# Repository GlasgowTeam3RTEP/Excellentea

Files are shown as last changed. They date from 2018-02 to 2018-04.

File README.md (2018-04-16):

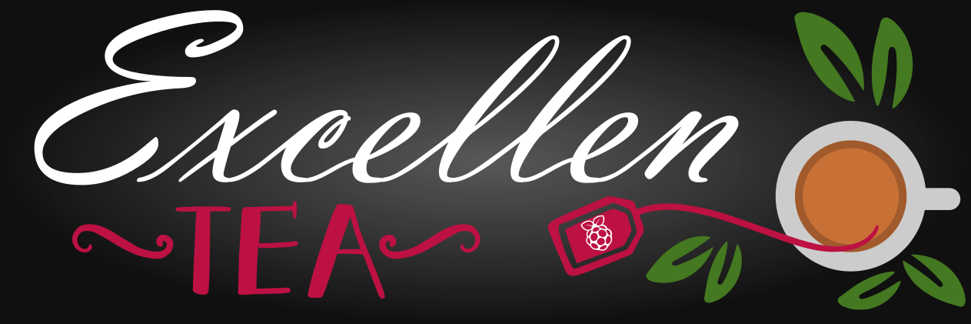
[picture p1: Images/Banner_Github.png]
Excellentea


# Description

Excellentea is an automatic tea maker. The user can operate the machine remotely through an online interface. 
In other words, you can order your tea, by chosing from several modes, as you leave work and find it ready when you get home. 
An LCD display provides feedback of the progress status. 

# Installation

## Prerequisites
The application requires the user to have Apache and php installed on their Raspberry Pi. Use your favourite package manager to install the packages _apache2_ and _php_ or, alternatively, open the terminal and use the commands below.
```
sudo apt-get update
sudo apt-get install apache2 php libapache2-mod-php -y
```
The One-wire and I2C protocols must be activated for the application to work. Run the following command:
```
sudo raspi-config
```
and navigate to _Interfacing options_ to enable _I2C_ and _1-Wire_.

## Installation procedure
Clone the repository to your Raspberry Pi and run the following commands:
```
./configure
make
make install
```
Initialise and start the apache web interface (change the default pi with your user name):
```
sudo chown -R pi /var/www/html/
rm /var/www/html/index.html
cp GUI/* /var/www/html/
sudo reboot
```
Find your local IP with:
```
hostname -I
```
The program can then be started by running the command
```
sudo excellentea
```
from the terminal, and the web interface will be available at the IP address found previously. The web interface can then be accessed by external hosts by enabling router port forwarding.

# Usage
[//]: # (instruct other people on how to use your project after they’ve installed it)

1. Load your cup with water

2. Load your tea infuser with the tea of your choice

3. Activate the tea maker from the online user interface

4. Choose the brewing mode of your tea

5. Wait...tea is ready:)

Watch Excellentea in action:
<p align="center">
<a href="http://www.youtube.com/watch?feature=player_embedded&v=Yk8ouI6cpxk
" target="_blank">Click to play</a>
</p>

# Configuration
An in-depth description of the project can be found on our [wiki](https://github.com/GlasgowTeam3RTEP/Excellentea/wiki). The following sections will briefly describe the main components and their implementation in the overall design. 

## Hardware

### Key components
- 1 Raspberry PI microcontroller board (tested on version 3 Model B)
- 1 Stepper motor (MIKROE-1530)
- 1 Digital temperature sensor (ds18b20)
- 12V DC power supply 
- 1 heating element (12V) (B004O8BGXE)
- 1 tea infuser 
- 1 reed float sensor (59630)
- 2 Darlington transistor array (ULN2803A)
- LCD
- 2 N-channel logic-level MOSFET (FQP30N06L)
- MOSFET heat sink (507222B00000G)

### Additional components
The project also requires standard passive components (e.g. resistors), prototyping tools (e.g. breadboard/pcb) and materials for the encasing. Check out our [wiki](https://github.com/GlasgowTeam3RTEP/Excellentea/wiki) for details. 

### Protocol
The digital temperature sensor DS18B20 communicates with the board through the one-wire protocol on pin 7 (BCM4). The reed float sensor only outputs two-states so a communication protocol is not required. 

## Software
The software was written to reflect the data flow depicted below. The float switch is used as a safety feature to ensure that the heating element cannot be switched on in the absence of water. Once the cup is full of water, the program will wait for a user interaction through the web interface. The main program will receive the signal to initiate the tea making procedure, using a temporary communication file, with two main parameters, the brewing temperature and the brewing time. The heating element is turned on and the temperature is monitored periodically via the sensor on the One-wire bus. Once the temperature reaches the desired value, the heating element is switched off and the preloaded tea infuser is lowered by the stepper motor. Once the desired brewing time has elapsed, the stepper motor rewinds the strainer and the tea is ready. Full software documentation can be found [here](https://glasgowteam3rtep.github.io/Excellentea/).

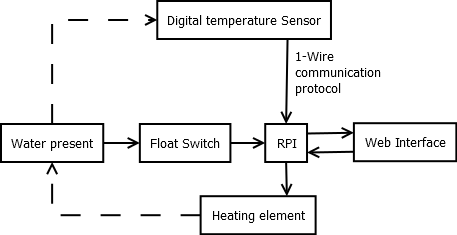
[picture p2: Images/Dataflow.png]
Data Flow Flow diagram of the tea maker


# Authors
* [**Andrea Spanou**](https://github.com/andreaspanou) - *Initial work* 
* [**Ciaran McGeady**](https://github.com/CiaranAnthony) - *Initial work*
* [**Simone Marcigaglia**](https://github.com/SimoneMarcigaglia) - *Initial work*

See also the list of [contributors](https://github.com/GlasgowTeam3RTEP/ExcellenTea/contributors) who participated in this project. Check out our [Twitter](https://twitter.com/Excellentea1) page to be up-to-date with the latest developments!

# Contributing

Please read [CONTRIBUTING.md](CONTRIBUTING.md) for details on our code of conduct, and the process for submitting pull requests to us.

# License

This project is licensed under the MIT License - see the [LICENSE](LICENSE) file for details.

# Acknowledgments

We would like to thank the weather in Glasgow for making us think about tea all the time.

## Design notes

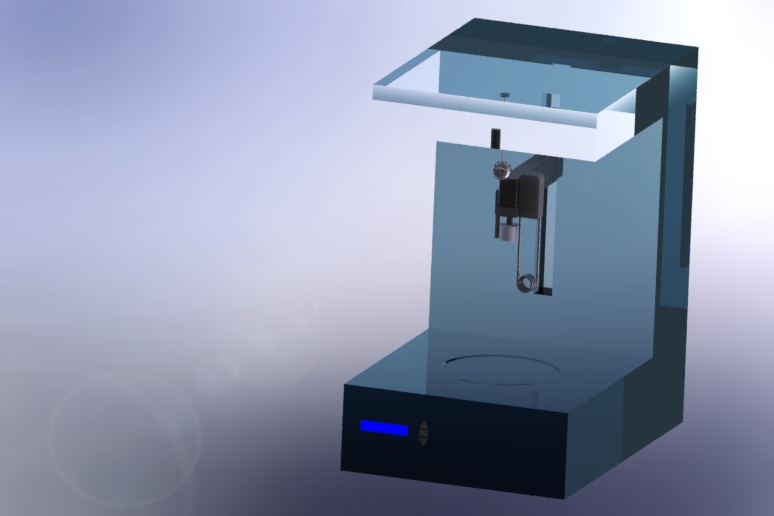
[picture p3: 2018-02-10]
Images/conceptual_design.JPG

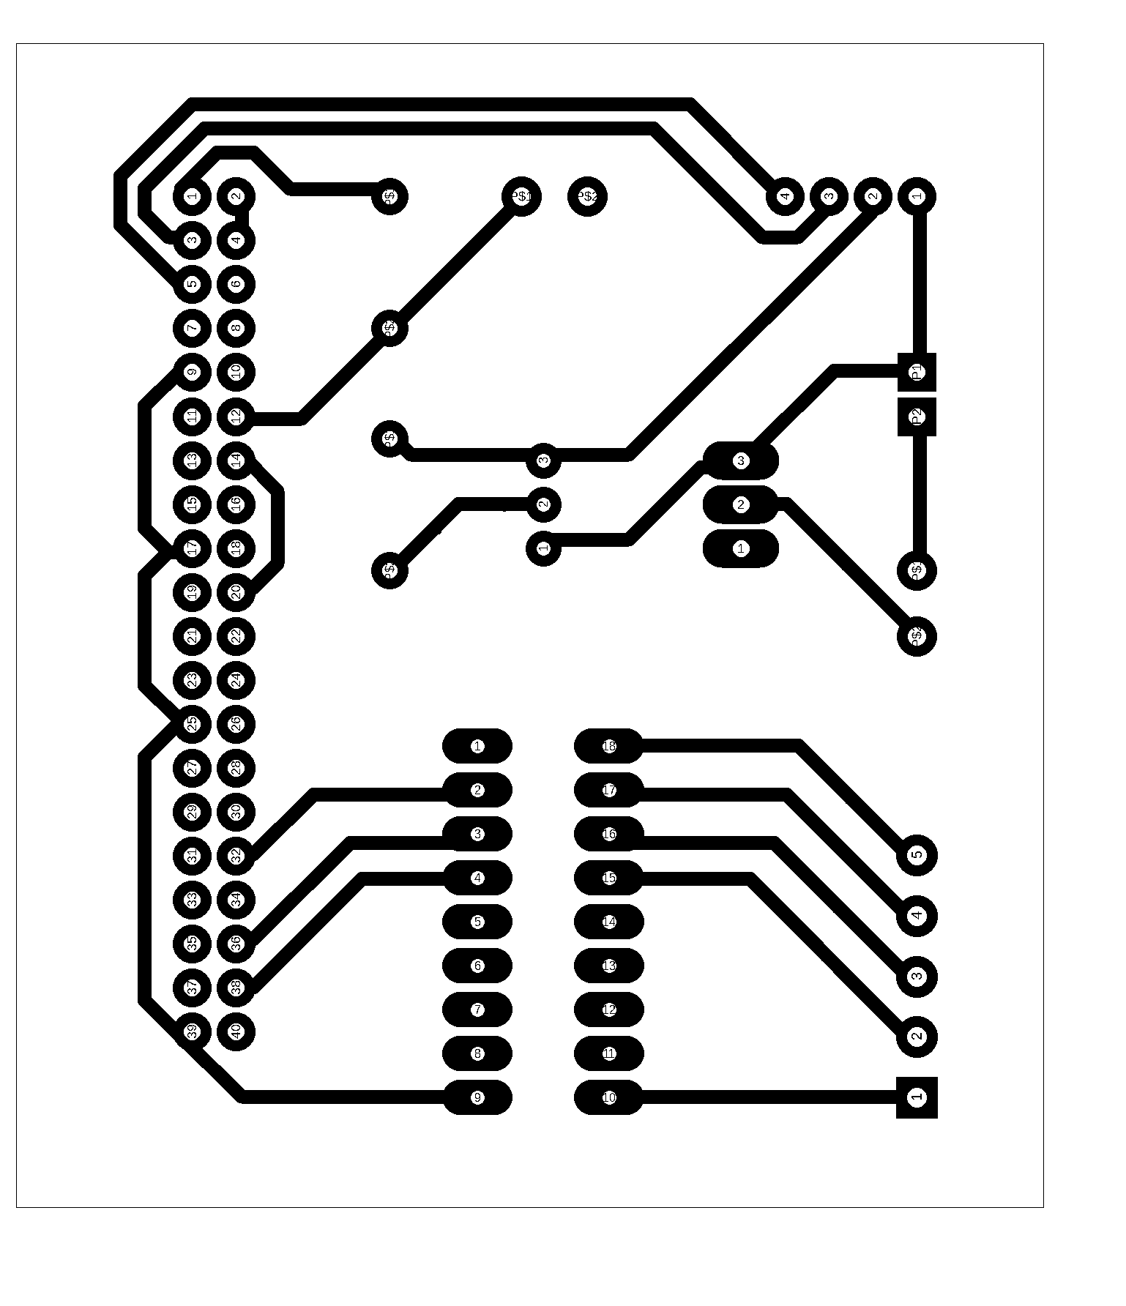
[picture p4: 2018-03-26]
Schematics/PCB_Top.png

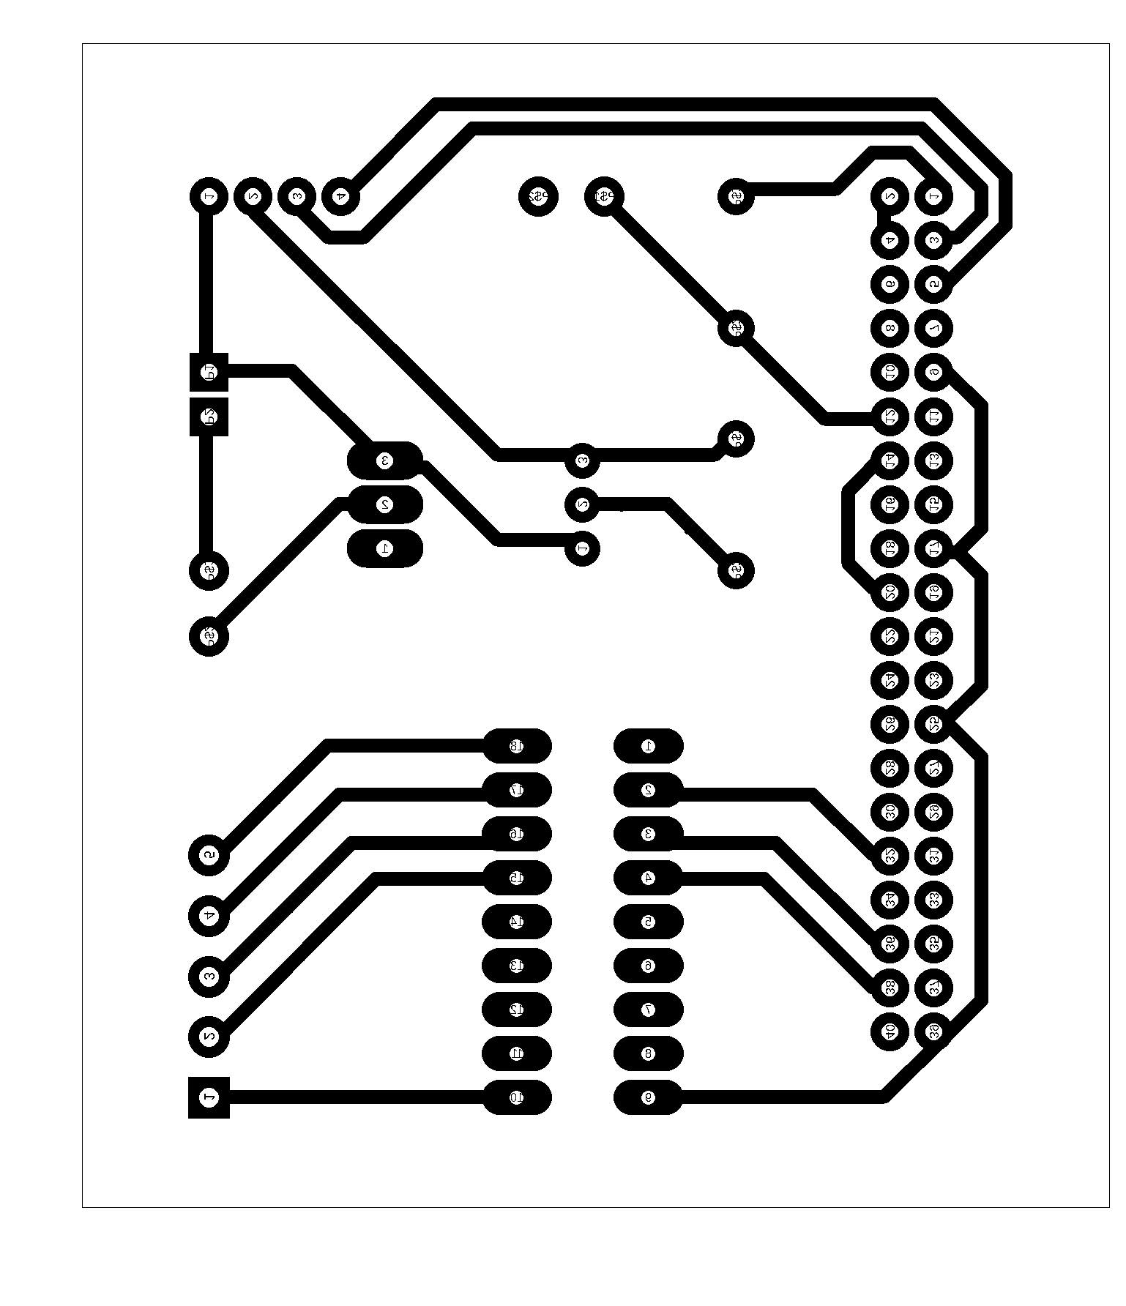
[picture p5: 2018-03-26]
Schematics/PCB_Top_mirrored.png

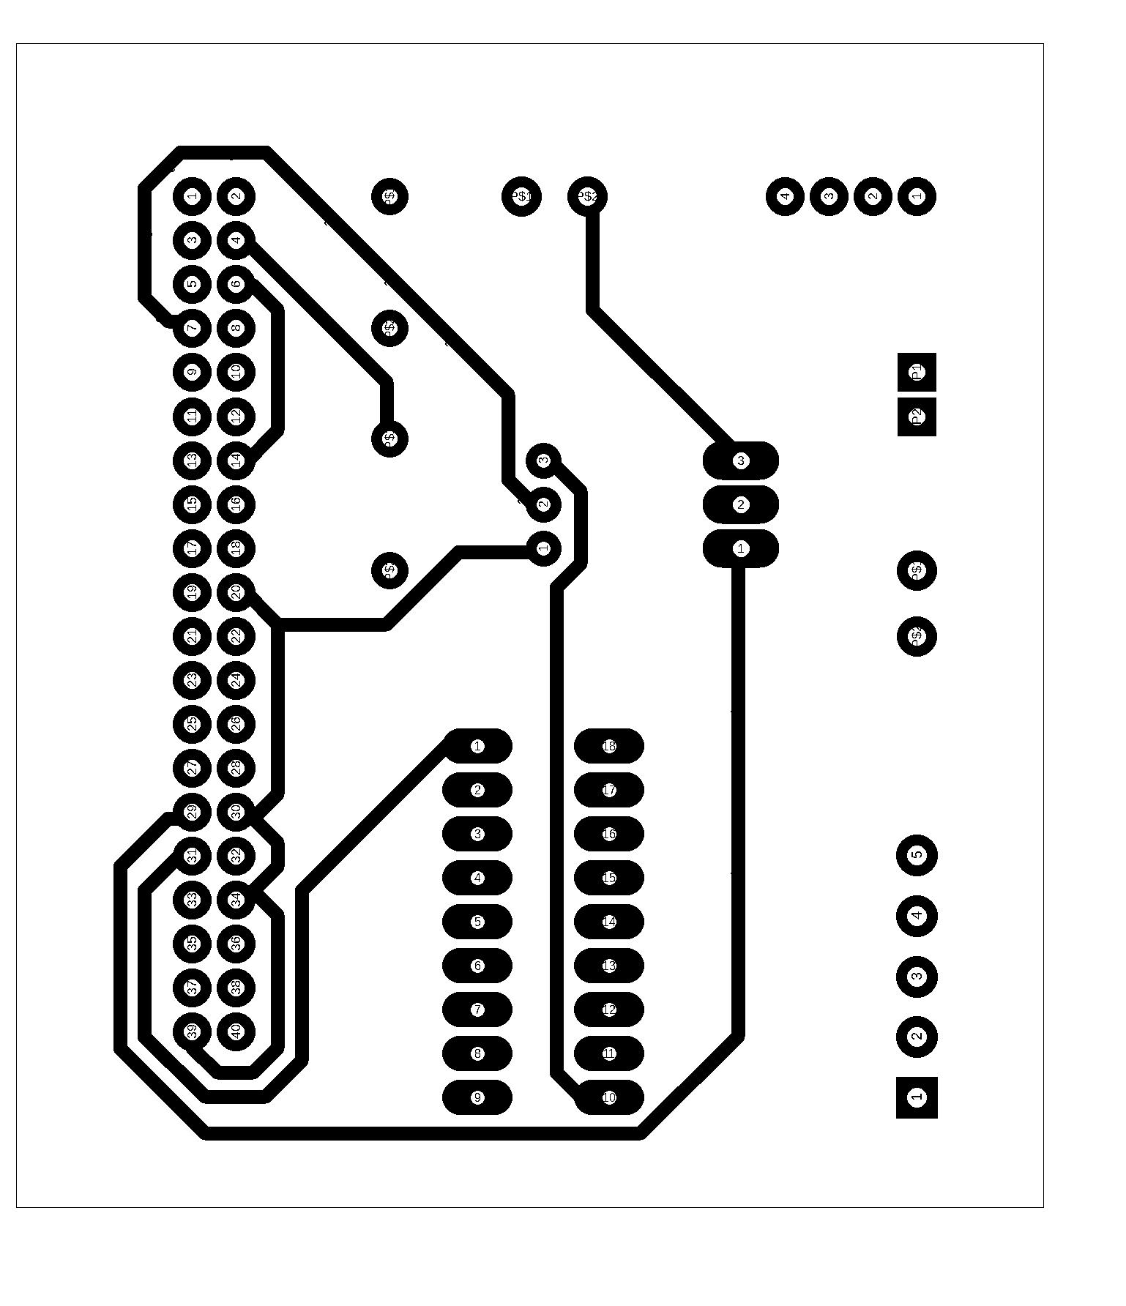
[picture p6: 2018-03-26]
Schematics/PCB_bottom.png

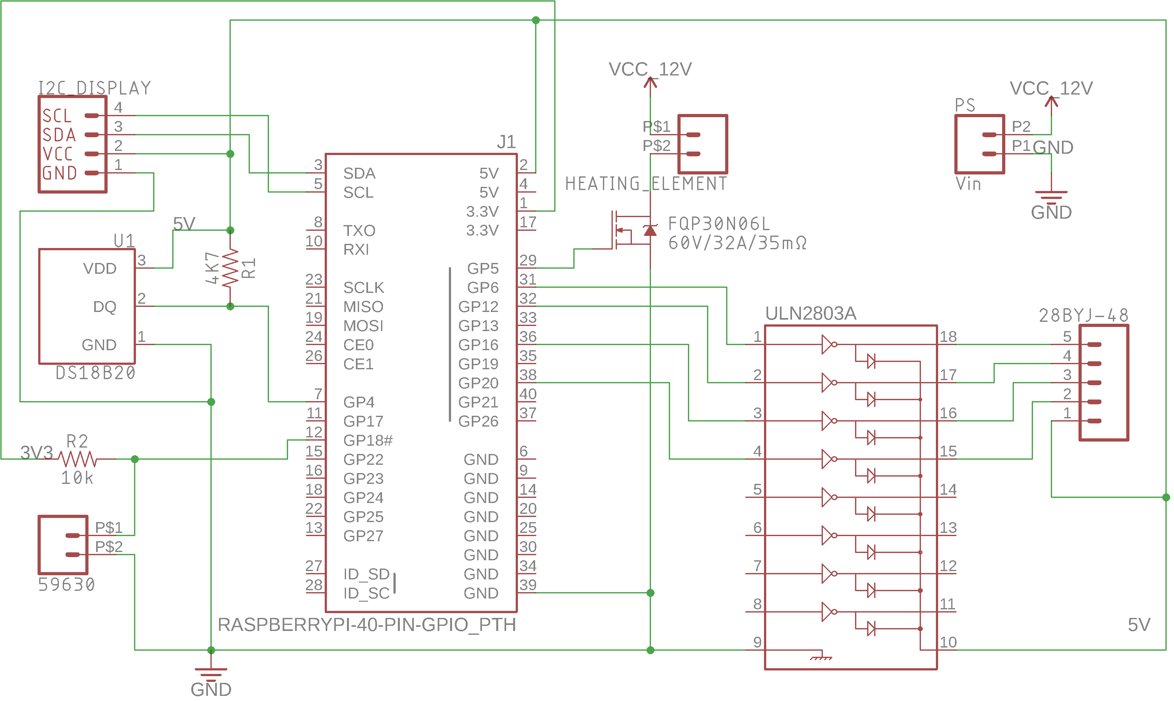
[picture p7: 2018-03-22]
Schematics/Schematics.png

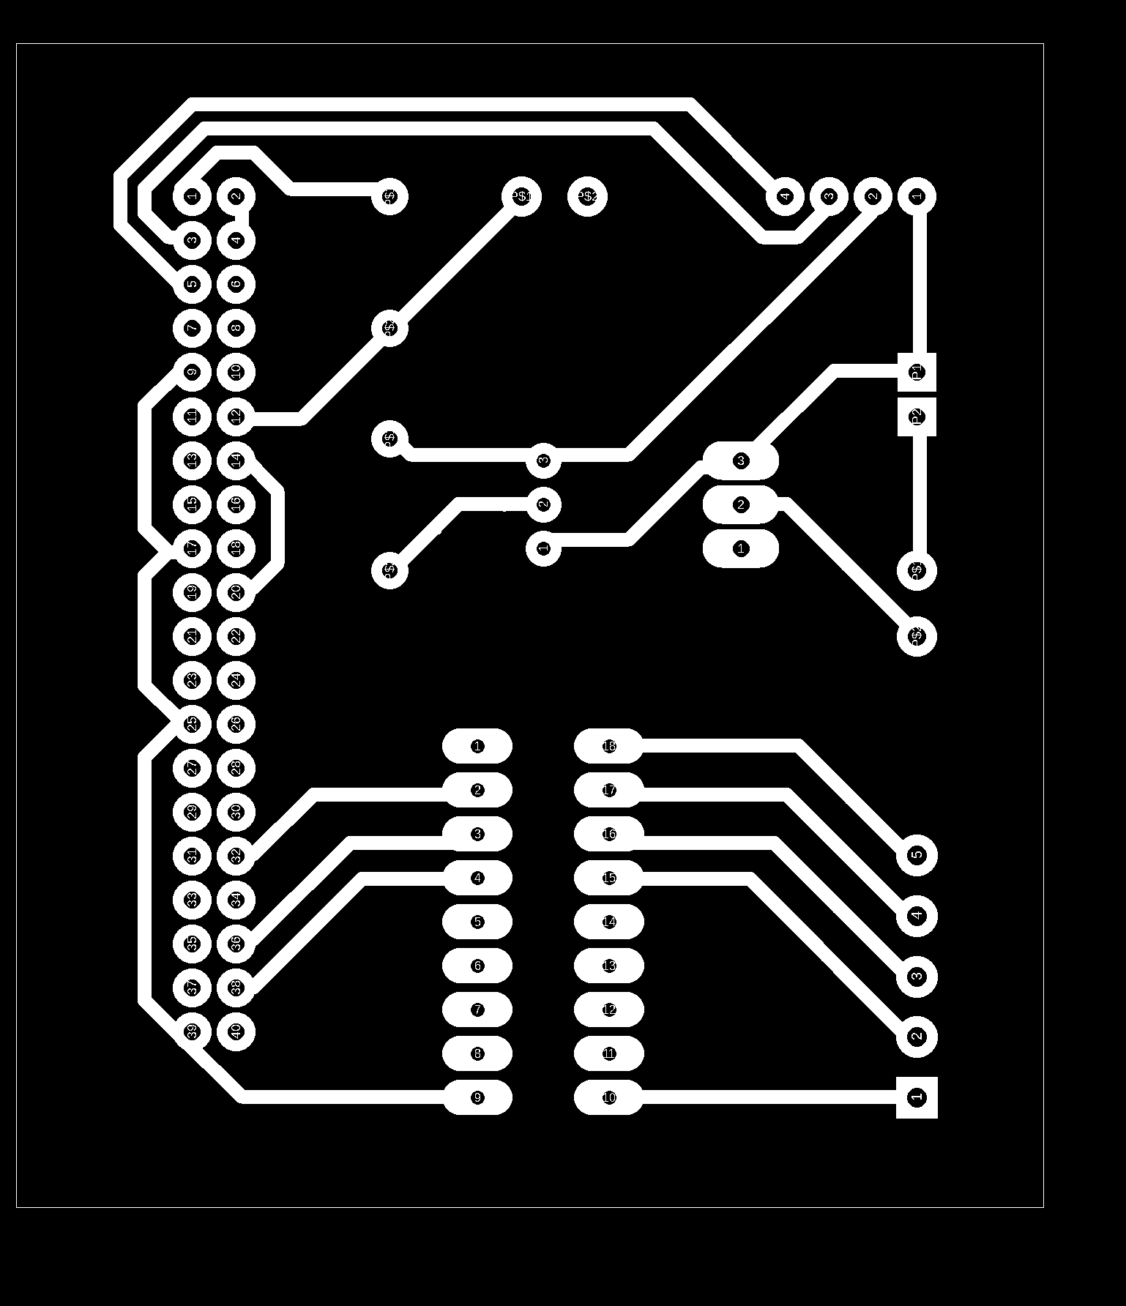
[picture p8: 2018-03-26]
Schematics/PCB_top.bmp

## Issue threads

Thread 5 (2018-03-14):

Directory layout

2073036n, 2018-03-14:
I would recommend placing the schematic files in a folder within your main project folder so that your main folder is neater and the schematics are easier to keep track of.

Team 11

SimoneMarcigaglia, 2018-03-18:
I have now moved the schematics in a subfolder. Thanks

Closed 2018-03-18.

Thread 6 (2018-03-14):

Software Information

croaljack0, 2018-03-14:
Further information about the software operation is required. i.e the different classes involved, number of threads of operation required.

** Team 10 **

SimoneMarcigaglia, 2018-03-26:
Our [wiki](https://github.com/GlasgowTeam3RTEP/Excellentea/wiki) has now been updated with that information. The full software documentation can be found [here](https://glasgowteam3rtep.github.io/Excellentea/index.html). Thanks for raising the issue.

Closed 2018-03-26.

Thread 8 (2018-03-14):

miss brief introduction about the code

jingwang9, 2018-03-14:
I don't get the point about the code, need brief introduction about the sensor's function

team 6

SimoneMarcigaglia, 2018-03-26:
A brief introduction of hardware and software can be found on our [wiki](https://github.com/GlasgowTeam3RTEP/Excellentea/wiki) and the full software documentation can be found [here](https://glasgowteam3rtep.github.io/Excellentea/). Thanks for raising the issue.

Closed 2018-03-26.

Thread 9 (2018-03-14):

Miss code, and software information

Kenny840394191, 2018-03-14:
I have not found your code, I think code will be required in your project. I hope to see more information about your sensors, will be better.

Team 15

SimoneMarcigaglia, 2018-03-26:
The code is now up on github. More information can be found on our [wiki](https://github.com/GlasgowTeam3RTEP/Excellentea/wiki) and in the [software documentation](https://glasgowteam3rtep.github.io/Excellentea/). Thanks for raising the issue.

Closed 2018-03-26.

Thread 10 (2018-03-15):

QT programming

gao540166030, 2018-03-15:
creates a QT widget for user interface

SimoneMarcigaglia, 2018-03-26:
We are using an I2C lcd only to display info on the machine. Qt is not required at this stage of the project, but it might be implemented as an additional feature in the future. Thanks for the suggestion.

Closed 2018-03-26.

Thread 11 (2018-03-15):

Temperature feedback program?

danmarwick, 2018-03-15:
I see that the programs within the "tea" folder take in user defined temperatures and the programs within the "sensor" folder read in temperature through the 1-wire protocol.  There should be a method for controlling the temperature of the heating element based on these two variables.

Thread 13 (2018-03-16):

Wiki page

acra6488, 2018-03-16:
Hi, Great project. I see there isn't much on the Wiki page yet. Would be a good place to put in more details on what problems you encountered and how you solved them when you get around to that stage.
-Aurelie -Team2

andreaspanou, 2018-03-25:
The wiki is now updated. More updates to come

Closed 2018-03-25.

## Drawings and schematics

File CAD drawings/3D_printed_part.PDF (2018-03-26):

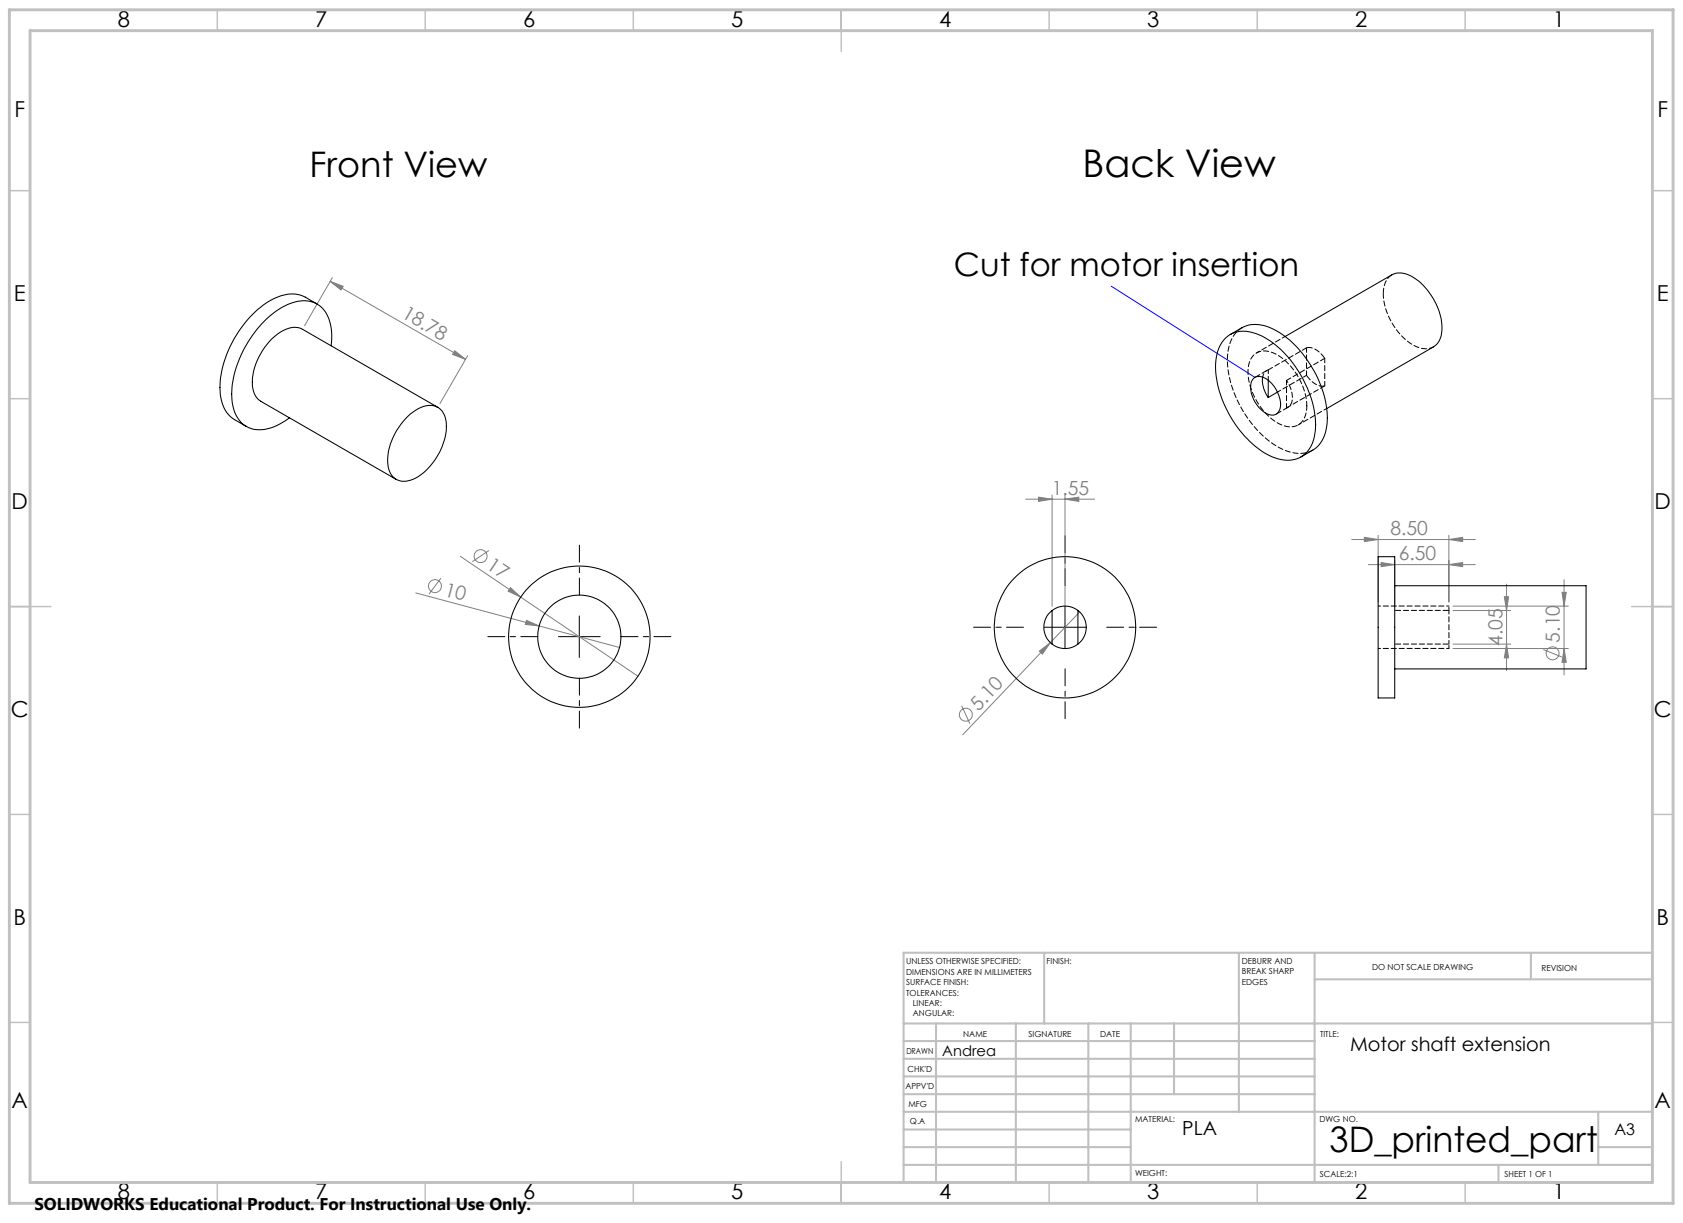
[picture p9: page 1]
Front View; Back View; FINISH:; DEBURR AND; BREAK SHARP; DO NOT SCALE DRAWING; REVISION; SCALE:2:1; SHEET 1 OF 1

Cut for motor insertion

UNLESS OTHERWISE SPECIFIED:
DIMENSIONS ARE IN MILLIMETERS
SURFACE FINISH:
TOLERANCES:
LINEAR:
ANGULAR:

NAME Andrea | SIGNATURE | DATE | | | | TITLE: Motor shaft extension

DRAWN
CHK'D
APPV'D
MFG
Q.A | | | | MATERIAL: PLA | DWG NO. 3D_printed_part | A3

SOLIDWORKS Educational Product. For Instructional Use Only.

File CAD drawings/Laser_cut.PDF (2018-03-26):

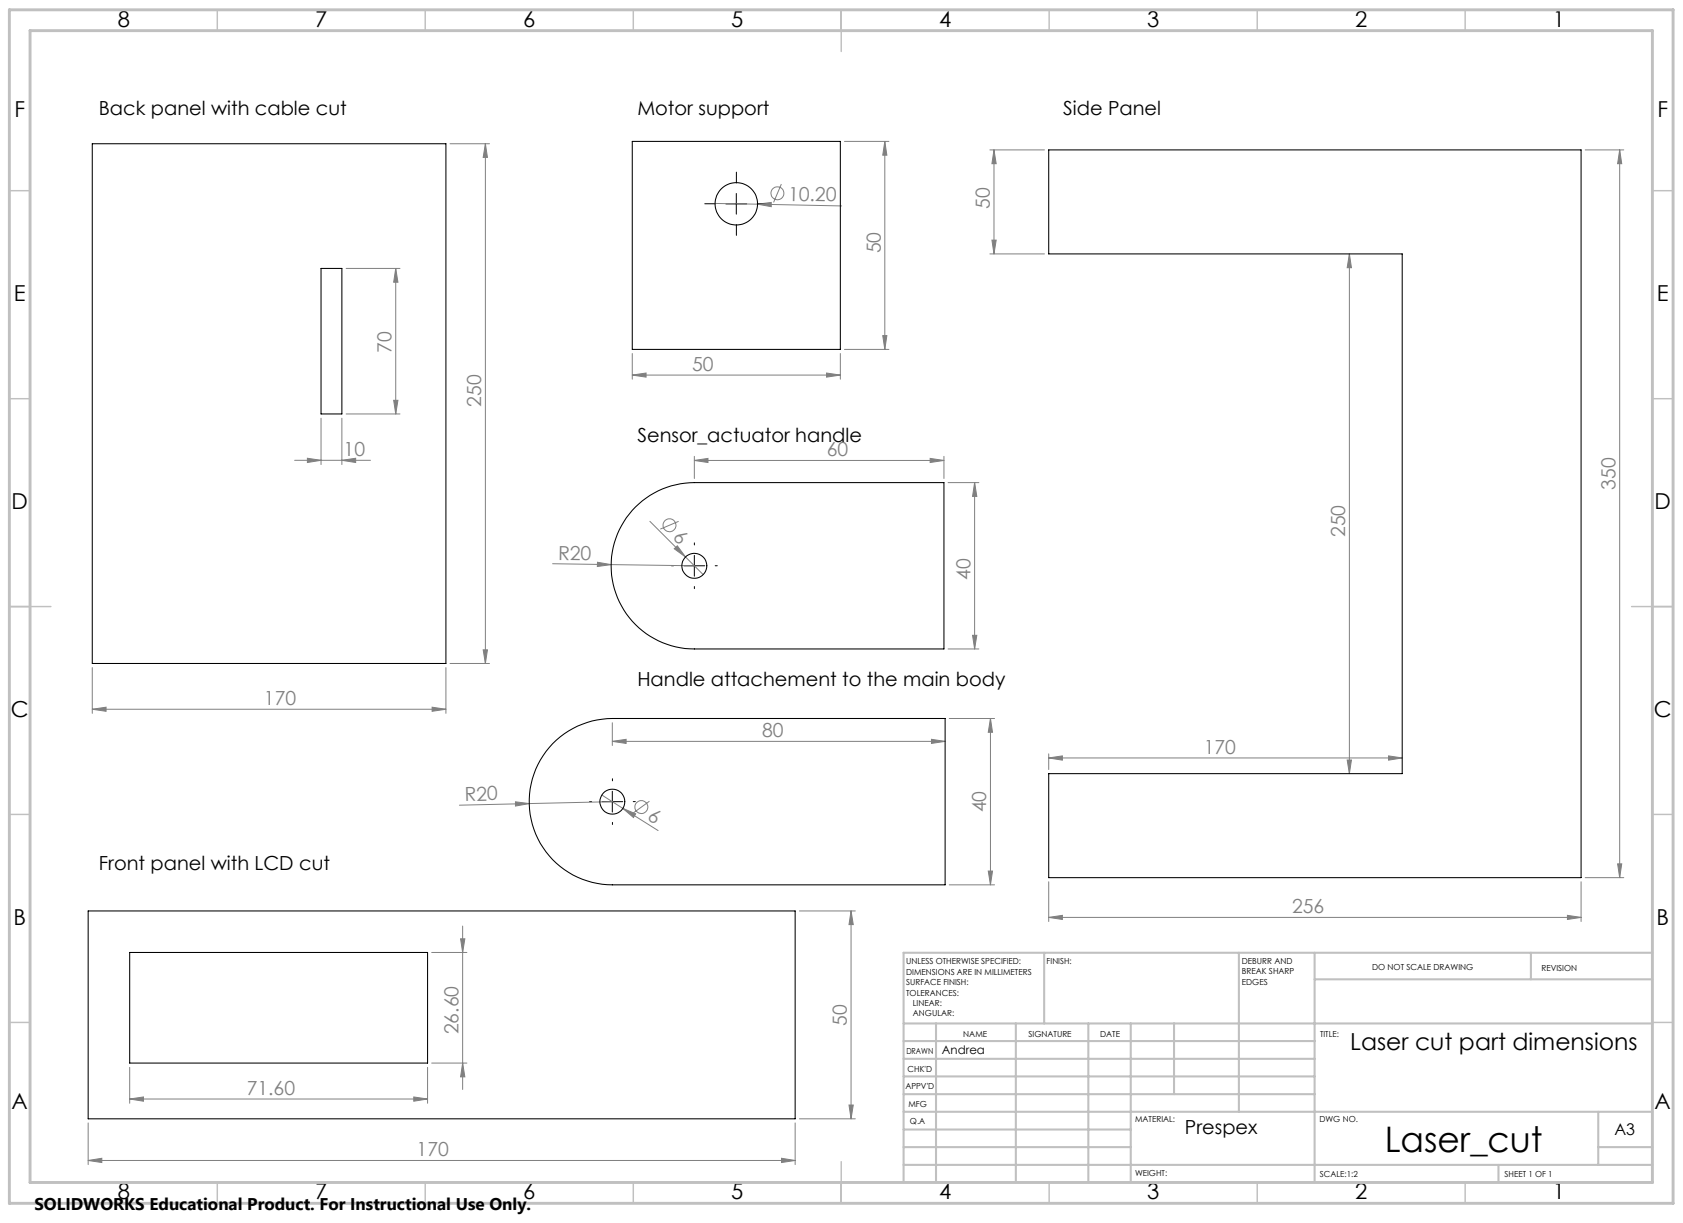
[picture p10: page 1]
Back panel with cable cut; Motor support; Side Panel; Sensor_actuator handle; FINISH:; DEBURR AND; BREAK SHARP; DO NOT SCALE DRAWING; REVISION; SCALE:1:2; SHEET 1 OF 1

Handle attachement to the main body

Front panel with LCD cut

UNLESS OTHERWISE SPECIFIED:
DIMENSIONS ARE IN MILLIMETERS
SURFACE FINISH:
TOLERANCES:
LINEAR:
ANGULAR:

Andrea NAME | SIGNATURE | DATE | | | | Laser cut part dimensions TITLE:

DRAWN
CHK'D
APPV'D
MFG
Q.A | | | | MATERIAL: Prespex | DWG NO. Laser_cut | A3

SOLIDWORKS Educational Product. For Instructional Use Only.

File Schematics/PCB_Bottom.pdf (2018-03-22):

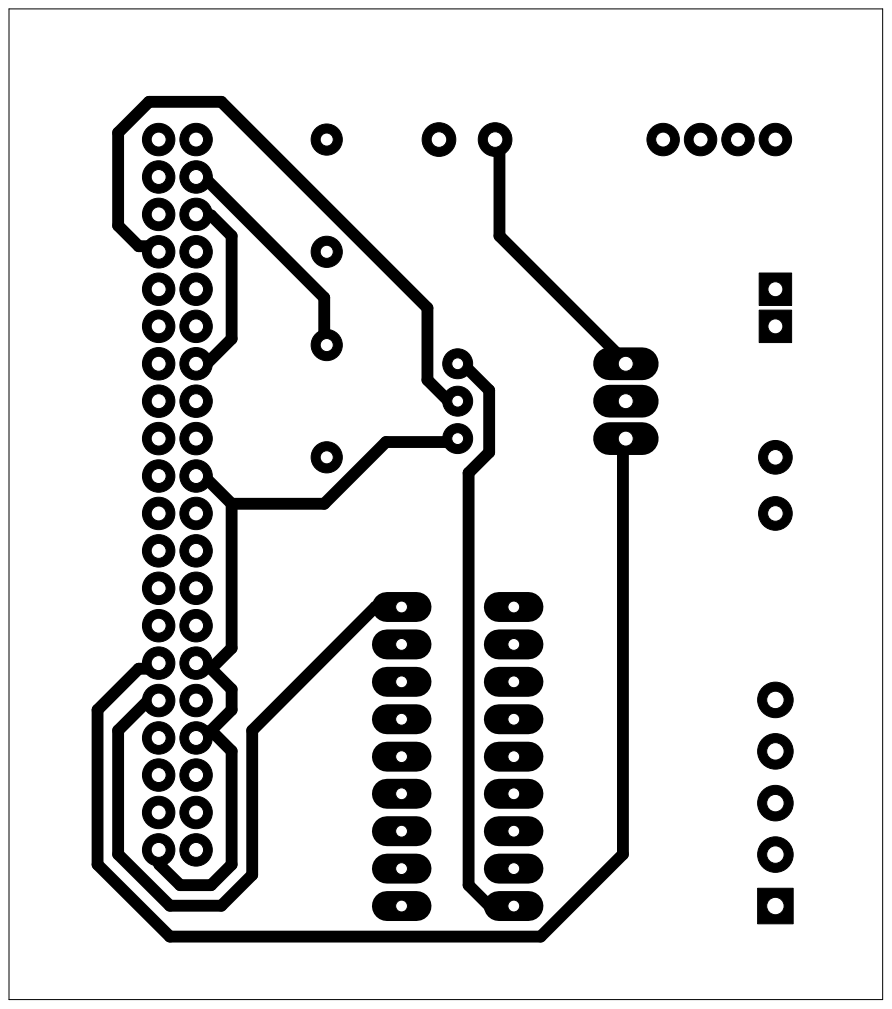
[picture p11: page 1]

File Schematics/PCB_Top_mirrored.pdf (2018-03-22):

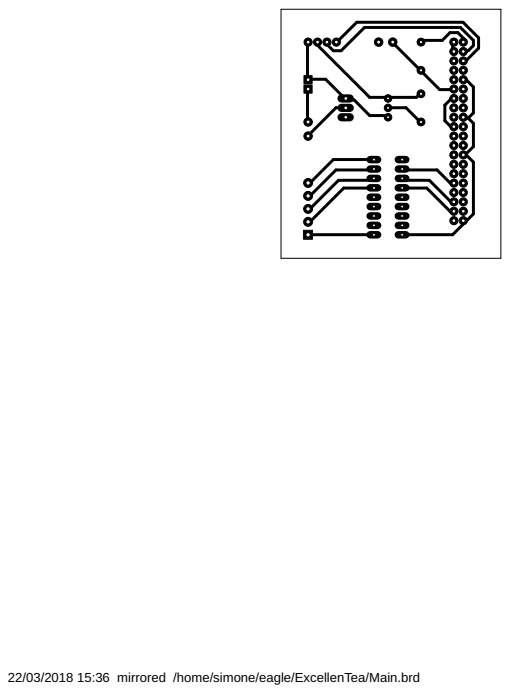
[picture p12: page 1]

22/03/2018 15:36 mirrored /home/simone/eagle/ExcellenTea/Main.brd

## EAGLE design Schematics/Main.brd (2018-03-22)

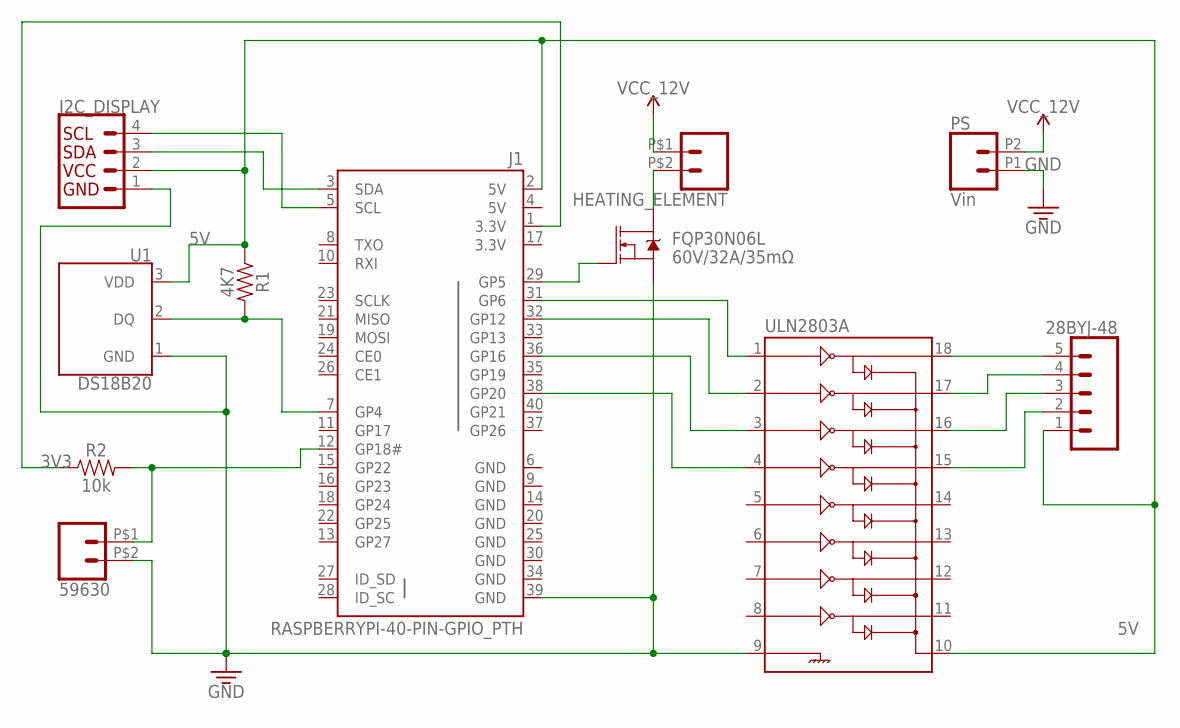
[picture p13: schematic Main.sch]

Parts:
28BYJ-48: CONN_05SCREW; SCREWTERMINAL-3.5MM-5
59630: CONN_02PTH2; 1X02_BIG
FQP30N06L: 60V/32A/35mΩ; TO220V
HEATING_ELEMENT: CONN_02PTH2; 1X02_BIG
I2C_DISPLAY: I2C_STANDARD; 1X04
J1: RASPBERRYPI-40-PIN-GPIO_PTH; 2X20_SHROUDED
PS: Vin; 1X02_2.54_SCREWTERM
R1: 4K7; AXIAL-0.3
R2: 10k; AXIAL-0.3
U1: DS18B20; TO-92-AMMO
ULN2803A: ULN2803DIP; DIL18

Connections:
3V3: J1.1 (3.3V), R2.P$1 (1)
5V: 28BYJ-48.1, I2C_DISPLAY.2, J1.2 (5V), J1.4 (5V), R1.P$1 (1), U1.3 (VDD), ULN2803A.10
12V: HEATING_ELEMENT.P$1 (1), PS.P2 (2)
DQ: J1.7 (GP4), R1.P$2 (2), U1.2 (DQ)
GND: 59630.P$2 (2), FQP30N06L.3 (S), I2C_DISPLAY.1, J1.6 (GND), J1.9 (GND), J1.14 (GND), J1.17 (3.3V), J1.20 (GND), J1.25 (GND), J1.30 (GND), J1.34 (GND), J1.39 (GND), PS.P1 (1), U1.1 (GND), ULN2803A.9
unnamed: J1.31 (GP6), ULN2803A.1
unnamed: FQP30N06L.1 (G), J1.29 (GP5)
unnamed: J1.36 (GP16), ULN2803A.3
unnamed: J1.38 (GP20), ULN2803A.4
unnamed: FQP30N06L.2 (D), HEATING_ELEMENT.P$2 (2)
unnamed: J1.32 (GP12), ULN2803A.2
unnamed: 28BYJ-48.5, ULN2803A.18
unnamed: 28BYJ-48.4, ULN2803A.17
unnamed: 28BYJ-48.3, ULN2803A.16
unnamed: 28BYJ-48.2, ULN2803A.15
SCL: I2C_DISPLAY.4, J1.5 (SCL)
SDA: I2C_DISPLAY.3, J1.3 (SDA)
WS: 59630.P$1 (1), J1.12 (GP18#), R2.P$2 (2)

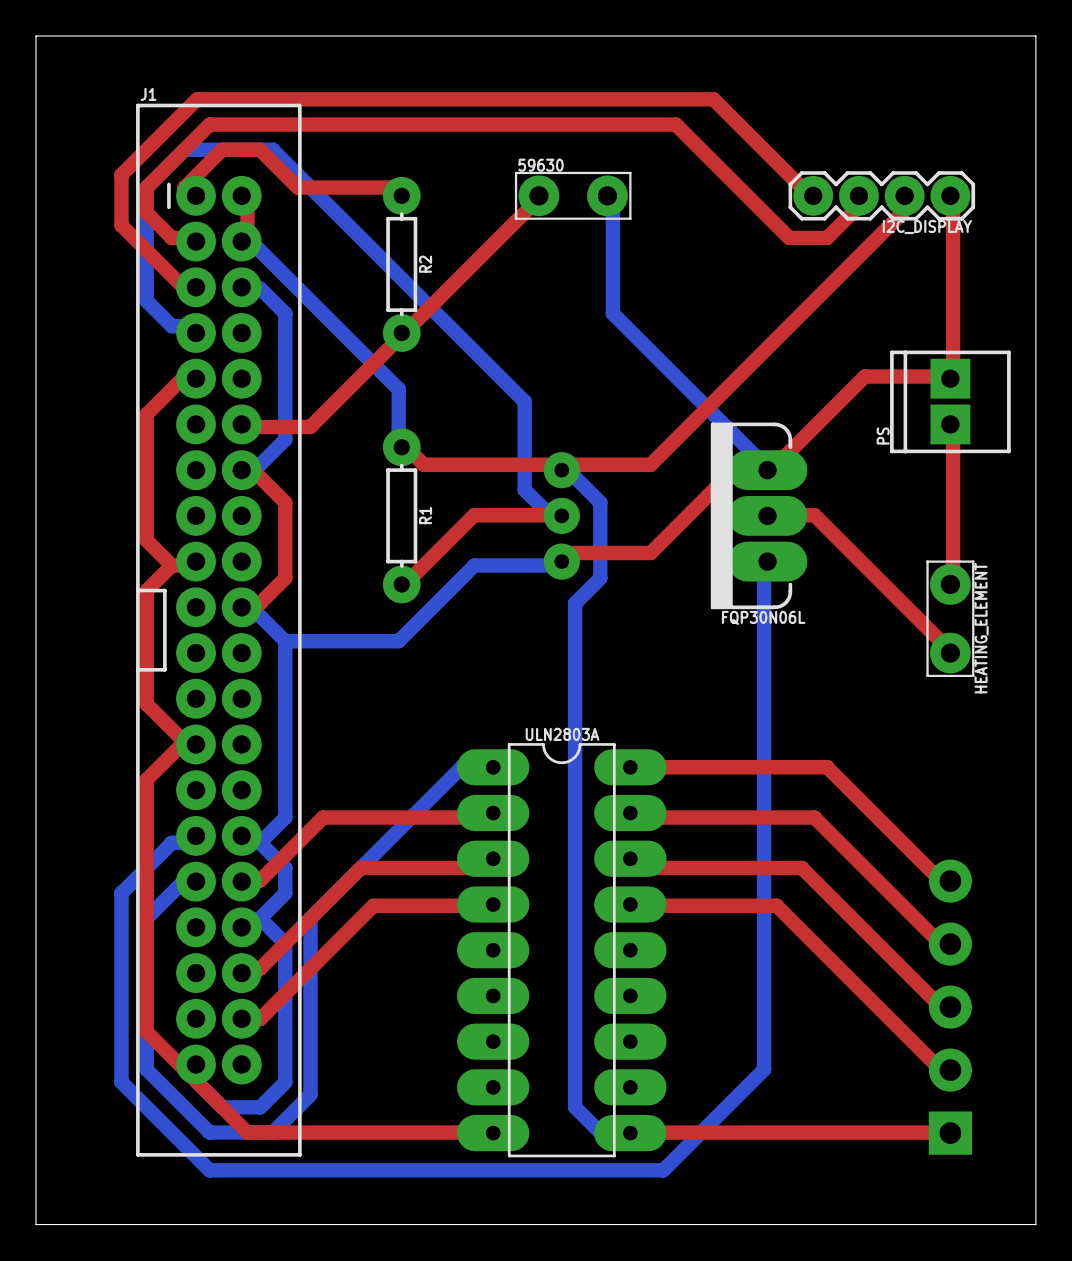
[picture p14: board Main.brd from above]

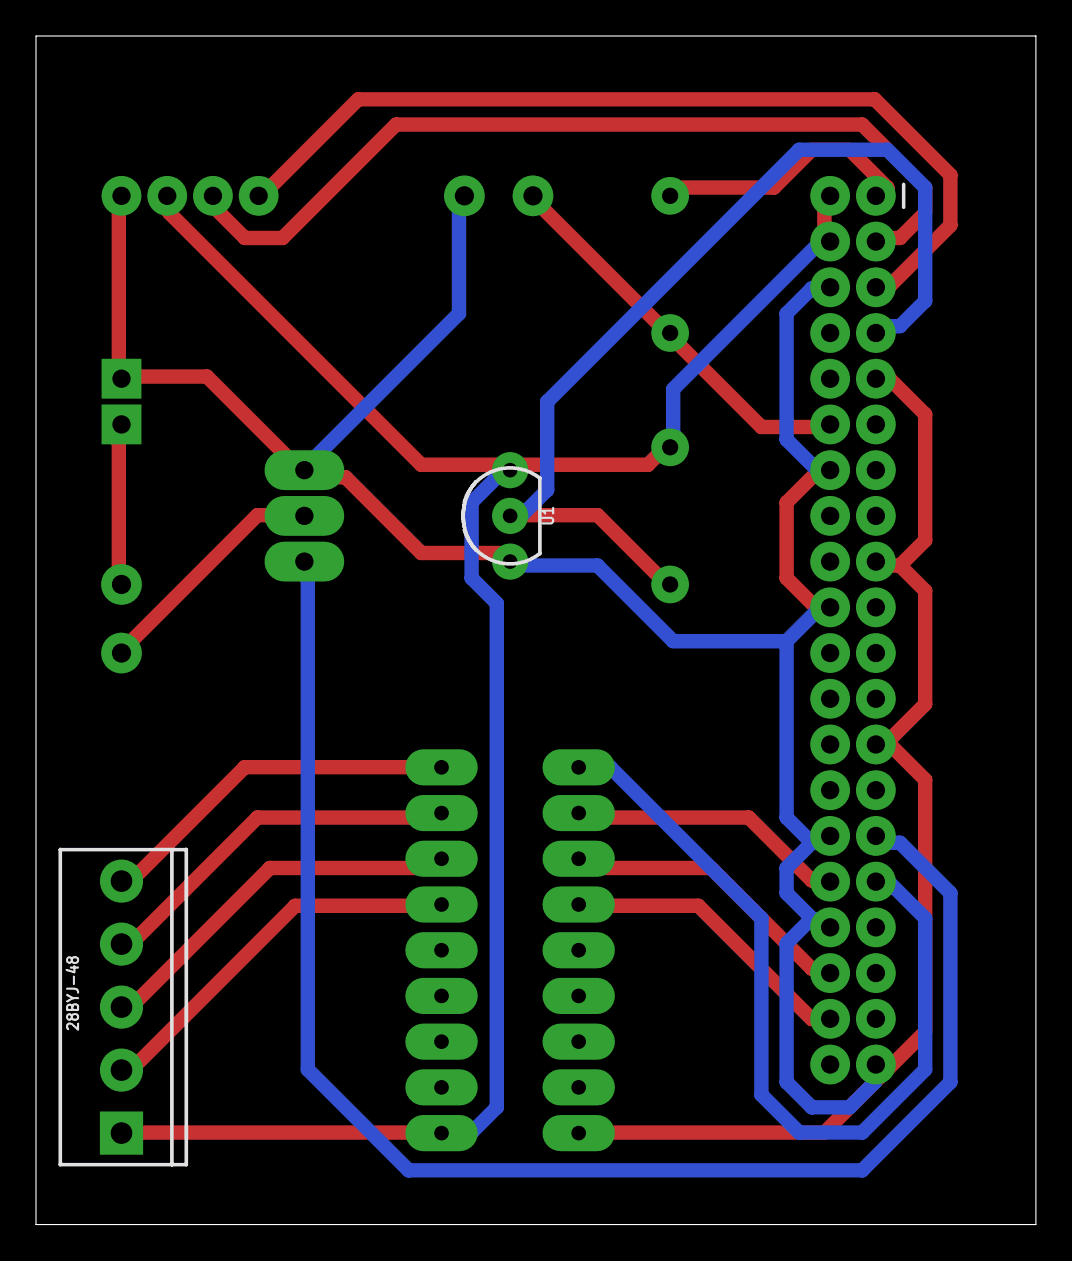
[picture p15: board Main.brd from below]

Board: 2 copper layers, 55.5 x 66.0 mm, 11 parts (2 on the bottom side), 18 nets.

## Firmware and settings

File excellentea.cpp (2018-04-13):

#include "Classes/Actuator.h"
#include "Classes/DS18B20.h"
#include "Classes/LiquidCrystal_I2C.h"
#include "Classes/Sensor.h"
#include "Classes/Stepper.h"
#include "Classes/Tea.h"

#include <chrono>
#include <ctime>
#include <fstream>
#include <iostream>
#include <iomanip>
#include <sstream>
#include <stdio.h>
#include <string>
#include <thread>

std::string readTag(std::string tag, std::string filename) {
	std::ifstream readFile(filename.c_str());
	std::string line = "";
	std::string fileTag = "";
	std::string fileValue = "";
	int pos = 0;

	while (getline(readFile, line)) {
		pos = line.find("\t");
		if (pos != 0) {
			fileTag = line.substr(0, pos);
			fileValue = line.substr(pos + 1);
			if (tag == fileTag) {

				return fileValue;
			}
		}
	}
	return "not found";
}

void writeTag(std::string tag, std::string value, std::string filename) {
	std::string tempFile = "writeTag.tmp";
	std::ifstream readFile(filename.c_str());
	std::ofstream writeFile(tempFile.c_str());
	std::string line = "";
	std::string fileTag = "";
	std::string fileValue = "";
	int pos = 0;
	bool replaced = false;

	while (getline(readFile, line)) {
		pos = line.find("\t");
		if (pos != 0) {
			fileTag = line.substr(0, pos);
			fileValue = line.substr(pos + 1);
			if (tag == fileTag) {
				line = fileTag + '\t' + value;
				replaced = true;
			}
			writeFile << line << std::endl;
		}
	}
	writeFile.close();
	readFile.close();

	if (replaced) {
		rename(tempFile.c_str(), filename.c_str());
		//allow apache to read and modify contents
		system("sudo chown -R www-data: /var/www/html");
	} else {
		remove(tempFile.c_str());
	}
}

int main() {

	//Define components***
	Sensor water_sensor(0); //PIN 12
	DS18B20 temp_sensor(7, "28-0516a06e58ff"); //PIN 7 and bus id
	Stepper strainer(24, 23, 22, 21, 64); //coils terminals and steps
	Actuator heat_elem(30);

	//Define Display connection***
	// i2c address
	uint8_t i2c = 0x27;
	// Control line PINs
	uint8_t en = 2;
	uint8_t rw = 1;
	uint8_t rs = 0;

	// Data line PINs
	uint8_t d4 = 4;
	uint8_t d5 = 5;
	uint8_t d6 = 6;
	uint8_t d7 = 7;

	// Backlight PIN
	uint8_t bl = 3;

	// LCD display size
	uint8_t rows = 2;
	uint8_t cols = 16;
	LiquidCrystal_I2C lcd("/dev/i2c-1", i2c, en, rw, rs, d4, d5, d6, d7, bl, POSITIVE);

	//Initialise components***
	water_sensor.initialise();
	temp_sensor.initialise();
	strainer.initialise();
	heat_elem.initialise();
	heat_elem.switchOff();
	lcd.begin(cols, rows);
	std::cout << "Initialisation complete!!" << std::endl;

	//Configurations file
	std::string configFile = "/var/www/html/config";

	//Turn on LCD
	lcd.on();
	std::ostringstream strs;
	while (1) {
		//Initialise config file
		writeTag("READY", "NO", configFile);
		writeTag("MAKE", "NO", configFile);
		writeTag("PROGR", "NO", configFile);
		writeTag("DONE", "NO", configFile);
		lcd.clear();
		
		//Check presence of water***
		while (1) {
			lcd.home();
			if (water_sensor.readStatus()) {
				//Print status on lcd
				lcd.print("Not ready      ");
				//change flag in configuration file
				if (readTag("READY", configFile) == "YES") {
					writeTag("READY", "NO", configFile);
				}
			} else {
				//Print status on lcd
				lcd.print("READY!         ");
				//change flag in configuration file
				if (readTag("READY", configFile) == "NO") {
					writeTag("READY", "YES", configFile);
				}
				if (readTag("MAKE", configFile) == "YES") {
					break;
				}
			}
			std::this_thread::sleep_for(std::chrono::milliseconds(1000));
		}

		//Read tea characteristics
		double desired_temp = std::stod(readTag("TEMP", configFile));
		double desired_time = std::stod(readTag("TIME", configFile));
		Tea myTea(desired_temp, desired_time);

		//Turn ON heating element***
		heat_elem.switchOn();
		lcd.clear();
		lcd.print("Activating...");

		//Update progress flag
		writeTag("PROGR", "YES", configFile);

		//Check water temperature***
		lcd.clear();
		lcd.print("Heating up...");
		std::cout<<"Heating up to "<< myTea.getBrewTemperature()<<"degrees."<<std::endl;
		while (temp_sensor.readTemp() < myTea.getBrewTemperature()) {
			lcd.setCursor(0, 1);
			strs << "T= " << std::setprecision(5) << temp_sensor.readTemp() << " C     ";
			lcd.print(strs.str().c_str());
			std::cout<<strs.str().c_str()<<std::endl;
			strs.str(std::string());
			std::this_thread::sleep_for(std::chrono::milliseconds(1000));
		}

		//Turn off heating element***
		heat_elem.switchOff();
		std::cout<<"Heating element OFF"<<std::endl;
		
		//Lower strainer***
		lcd.clear();
		lcd.print("Lowering");
		lcd.setCursor(0,1);
		lcd.print("strainer");
		std::cout<<"Strainer DOWN"<<std::endl;
		strainer.spin(350, 30, 0);
		
		//Sleep for brewing time***
		lcd.clear();
		lcd.print("Brewing...");
		std::cout<<"Brewing"<<std::endl;
		int duration = myTea.getBrewTime() * 60 ;
		
		
		clock_t begin = clock();
		double time_elapsed = 0;
		double time_left = 0;
		int minutes_left = 0;
		int seconds_left = 0;
		
		while ((double(clock()-begin)/ CLOCKS_PER_SEC*1000)<duration) {
			time_elapsed = double(clock()-begin)/ CLOCKS_PER_SEC*1000;
			time_left = duration - time_elapsed;
			minutes_left = time_left/60;
			seconds_left = (time_left/60 - (double(minutes_left)))*60;
			
			strs <<minutes_left<<":"<<seconds_left<<"      ";
			lcd.setCursor(0,1);
			lcd.print(strs.str().c_str());
			std::cout<<strs.str().c_str()<< "left"<<std::endl;
			strs.str(std::string());
			std::this_thread::sleep_for(std::chrono::milliseconds(1000));
		}
  
		//Pull-up strainer***
		lcd.clear();
		lcd.print("Pulling up");
		lcd.setCursor(0,1);
		lcd.print("strainer");
		std::cout<<"Strainer UP"<<std::endl;
		strainer.spin(350, 60,1);

		//Update on progress***
		lcd.clear();
		lcd.print("Your tea is");
		lcd.setCursor(0, 1);
		lcd.print("ready!!!");
		std::cout<<"FINISHED"<<std::endl;
		writeTag("DONE", "YES", configFile);
		std::this_thread::sleep_for(std::chrono::milliseconds(3 * 60 * 1000));
	}
}

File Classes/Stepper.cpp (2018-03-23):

#include "Stepper.h"
#include <wiringPi.h>

Stepper::Stepper(short A1, short A2, short B1, short B2, int steps)
{
	coil_A_pin_1 = A1;
	coil_A_pin_2 = A2;
	coil_B_pin_1 = B1;
	coil_B_pin_2 = B2;
	motor_steps = steps;
}

void Stepper::initialise()
{
	wiringPiSetup();

	pinMode(coil_A_pin_1, OUTPUT);
	pinMode(coil_A_pin_2, OUTPUT);
	pinMode(coil_B_pin_1, OUTPUT);
	pinMode(coil_B_pin_2, OUTPUT);
}

void Stepper::setStep(bool w1, bool w2, bool w3, bool w4)
{
	digitalWrite(coil_A_pin_1, w1);
	digitalWrite(coil_A_pin_2, w2);
	digitalWrite(coil_B_pin_1, w3);
	digitalWrite(coil_B_pin_2, w4);
}

void Stepper::forwardRun(int interval, int revolutions)
{
	for (int i = 0; i < motor_steps*revolutions; i++)
	{
		setStep(1, 0, 1, 0);
		delay(interval);
		setStep(0, 1, 1, 0);
		delay(interval);
		setStep(0, 1, 0, 1);
		delay(interval);
		setStep(1, 0, 0, 1);
		delay(interval);
	}
}

void Stepper::backwardRun(int interval, int revolutions)
{
	for (int i = 0; i < motor_steps*revolutions; i++)
	{
		setStep(1, 0, 0, 1);
		delay(interval);
		setStep(0, 1, 0, 1);
		delay(interval);
		setStep(0, 1, 1, 0);
		delay(interval);
		setStep(1, 0, 1, 0);
		delay(interval);
	}
}

void Stepper::spin(int speed, int revolutions, bool direction)
{
	int interval = 1000.0/speed;
	if (direction)
	{
		forwardRun(interval, revolutions);
	} else
	{
		backwardRun(interval, revolutions);
	}
}

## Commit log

2018-02-14 Added Circuit schematics and PCB design
    [Main.brd, Main.sch]
2018-03-14 Added classes (tea, stepper, sensor and ds18b20), makefile and configure file
2018-03-15 Moved circuit and board schematics to subfolder
    [Main.brd, Main.sch]
2018-03-22 Updated circuit schematics
    [Main.brd, Main.sch]
2018-03-22 Added float sensor and I2C LCD
    [Main.brd, Main.sch]
2018-03-23 Renamed folders for consistency
    [Main.brd, Main.sch]
2018-03-23 Added class to control heating element
2018-03-24 Added drawing for 3D printed part
2018-03-24 Added data flow diagram
2018-03-26 Added I2C lcd control and multi-thread programming
2018-03-26 Implemented multi-thread programming
2018-03-26 Converted PCB design to png
2018-03-26 Moved data flow
2018-04-04 Added webGUI comm and modified temperature feedback
2018-04-09 Removed multi-thread programming
2018-04-10 Added brewing countdown timer
2018-04-13 Changed pins to match circuit shematics

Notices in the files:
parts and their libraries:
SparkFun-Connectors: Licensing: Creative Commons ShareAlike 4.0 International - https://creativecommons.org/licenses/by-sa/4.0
